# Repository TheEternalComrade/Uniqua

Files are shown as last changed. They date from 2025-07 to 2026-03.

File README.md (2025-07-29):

# Uniqua
Uniqua is very cool pen plotter. She has 2 y-axis' to increase stability, limit switches for automatic homing, and a very good sense of style.
This is the most complex project I have ever undertaken, despite the relatively off-the-shelf electronics setup. The CAD is completely custom

## CAD


## Wiring


Credits to [Krishna Kumar](https://www.hackster.io/kk1211114) for the diagram

## BOM
| Name | Purpose | Source | Price | Link | Total|
|:---|:---|:---|:---|:---|:---|
|6pcs 8*400 Linear Rods|For bearings to slide on|Amazon|$27|[link](https://www.amazon.com/gp/product/B0CXTX5FZ3/ref=ox_sc_act_title_1?smid=A2IW11PEFKCHE9&psc=1)||
|Power Supply|To give arduino power|Amazon|$7.50|[link](https://www.amazon.com/gp/product/B018OLREG4/ref=ox_sc_act_title_3?smid=A2VN47FGA6FR8&psc=1)||
|GT2 stepper motor pulley|To hold belt|Amazon|$6|[link](https://www.amazon.com/gp/product/B07CXSSGF8/ref=ox_sc_act_title_4?smid=A2QQQKMKGVNA5E&psc=1)||
|Linear ball bearings|To enable smooth movement of gantries|Amazon|$12|[link](https://www.amazon.com/gp/product/B087WPGQ8T/ref=ox_sc_act_title_5?smid=A3TIH0U3DL7GNQ&psc=1)||
|Taxes|So the government gets a cut too|Amazon|$1.9|none||
|SG90 Servo| To lift pen|Aliexpress|$2.31|[link](https://www.aliexpress.com/item/3256806385982254.html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)||
|FTM Jumper Cables|To connext electronics wires|Aliexpress|$2.90|[link](https://www.aliexpress.com/item/3256802798368625.html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)||
|Arduino Uno Clone(extra in case of malfunction)|The brains|Aliexpress|$9|[link](https://www.aliexpress.us/item/3256805955372826.html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)||
|GT2 Idler pulley|To hold belt|Aliexpress|$3.51|[link](https://www.aliexpress.com/item/3256805966224219.html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)||
|M3 x 16 screws|to hold stepper motors|Aliexpress|$1.19|[link](https://www.aliexpress.com/item/3256805692722422.html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)||
|M5 x 20 screws|to hold idler pulleys|Aliexpress|$1.79|[link](https://www.aliexpress.com/item/2255800598515019.html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)||
|Stepper motor driver|to drive stepper motors|Aliexpress|$6.30|[link](https://www.aliexpress.com/item/3256803799187214.html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)||
|CNC shield| has all the works for safe cnc-ing|Aliexpress|$2.33|[link](https://www.aliexpress.us/item/3256806291794239.html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)||
|4 x 100 linear rod|For the pen holder to slide up|Aliexpress|$4.26|[link](https://www.aliexpress.com/item/3256804855023250.html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)||
|Limit switch|Automatic homing|Aliexpress|$1.58|[link](https://www.aliexpress.com/item/3256805410237576.html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)||
|M5 washers|So pulleys don't directly touch the plastic|Aliexpress|$1.68|[link](https://www.aliexpress.com/item/3256807003597592.html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)||
|m5 hex nuts|for m5 screws |Aliexpress|$2|[link](https://www.aliexpress.com/item/3256808093729366.html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)||
|gt2 timing belt|to move gantries|Aliexpress|$3.6|[link](https://www.aliexpress.com/item/3256808671441858.html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)||
|nema 17 stepper motor|to move belts|Aliexpress|$12.9|[link](https://www.aliexpress.com/item/3256805095424554.html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)||
|M8 x 500 threaded rod|To enhance stability|Aliexpress|$14.7|[link](https://www.aliexpress.com/item/3256807919274570.html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)||
|5 x 15 Spring|For more consistent pen contact|Aliexpress|$2.43|[link](https://www.aliexpress.com/item/3256807406561228.html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)||
|m8 hex nuts|for m8 rods|Aliexpress|$2.43|[link](https://www.aliexpress.com/item/3256807407546447.html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)|
|*m2 x 10 screw|For pen lift mechanism and fastening limit switches|Aliexpress|$~1.5|none||
|*m2 x 3 heatset inset|For holding screws|Aliexpress|~$1.5|none||
|Taxes|governments|Aliexpress|$6|||
||||||$134.88|

*Already have these

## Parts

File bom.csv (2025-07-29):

Name | Purpose | Source | Price | Link | Total
6pcs 8*400 Linear Rods | For bearings to slide on | Amazon | $27 | link
Power Supply | To give arduino power | Amazon | $7.50 | link
GT2 stepper motor pulley | To hold belt | Amazon | $6 | link
Linear ball bearings | To enable smooth movement of gantries | Amazon | $12 | link
Taxes | So the government gets a cut too | Amazon | $1.9 | none
SG90 Servo | To lift pen | Aliexpress | $2.31 | link
FTM Jumper Cables | To connext electronics wires | Aliexpress | $2.90 | link
Arduino Uno Clone(extra in case of malfunction) | The brains | Aliexpress | $9 | link
GT2 Idler pulley | To hold belt | Aliexpress | $3.51 | link
M3 x 16 screws | to hold stepper motors | Aliexpress | $1.19 | link
M5 x 20 screws | to hold idler pulleys | Aliexpress | $1.79 | link
Stepper motor driver | to drive stepper motors | Aliexpress | $6.30 | link
CNC shield | has all the works for safe cnc-ing | Aliexpress | $2.33 | link
4 x 100 linear rod | For the pen holder to slide up | Aliexpress | $4.26 | link
Limit switch | Automatic homing | Aliexpress | $1.58 | link
M5 washers | So pulleys don't directly touch the plastic | Aliexpress | $1.68 | link
m5 hex nuts | for m5 screws | Aliexpress | $2 | link
gt2 timing belt | to move gantries | Aliexpress | $3.6 | link
nema 17 stepper motor | to move belts | Aliexpress | $12.9 | link
M8 x 500 threaded rod | To enhance stability | Aliexpress | $14.7 | link
5 x 15 Spring | For more consistent pen contact | Aliexpress | $2.43 | link
m8 hex nuts | for m8 rods | Aliexpress | $2.43 | link
*m2 x 10 screw | For pen lift mechanism and fastening limit switches | Aliexpress | $~1.5 | none
*m2 x 3 heatset inset | For holding screws | Aliexpress | ~$1.5 | none
Taxes | governments | Aliexpress | $6
 |  |  |  |  | $134.88

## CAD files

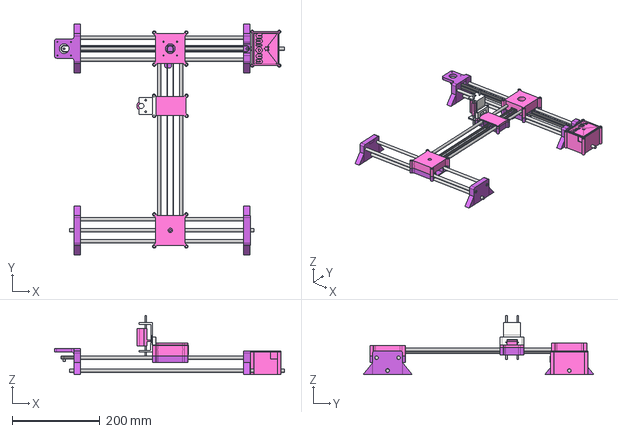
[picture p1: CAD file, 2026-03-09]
The-Scheme-Machine.step
524.0 x 526.0 x 134.4 mm

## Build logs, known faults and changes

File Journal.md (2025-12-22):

---
title: "Uniqua"
author: "@Ayo"
description: "A pen plotter for plotting schemes!"
created_at: "2025-05-30"
---

#Total Time Spent: 37 hours

## May 30, 2025
Today, I started brainstorming. Imma be honest, I feel completely out of my depth with this one.
With a keyboard, there are plenty of resources, and I had completed Hackpad before to boot.

I'm not sure where to start. 

So, I've taken to gobbling up every resource I can find about pen plotters.

Here are some I've found so far:

From Aliexpress


By [SuperbTech](https://www.instructables.com/member/Superb+Tech/)



By [Dejan](https://howtomechatronics.com/author/howtom12_wp/)

Learning about and examining these designs, I'm starting to see a rough bill of materials:
- 2 stepper motors for the x and y axis
- A servo motor to lift and place the pen
- 6 linears rods, 4 for the y axis, 2 for the x axis
- 4 to 8 linear ball bearing(these are kinda expensive)
- 2 stepper motor drivers
- A CNC shield
- A elegoo uno(cheaper than arduino)
- A 12v power supply

One resource I found particularly helpful was [this plotter](https://www.youtube.com/watch?v=z4_OFkAW_JY&ab_channel=CreativityBuzz) 
designed with wood instead of plastic parts. I found that the design was a lot simpler without any of the frills plastic parts had. 
This was extremely useful in helping me get an idea of how to design the toolhead.

After a lot of YouTube videos, I sketched out a more detailed plan for The Scheme Machine. I wish I could say I had an intuitive goal for this, like I had convenience
for The Prince Keeb, but I just want this to work TT.



Time Spent: 5 hours

## June 4, 2025
I've placed the first item in my 3d model! A humble Nema 42-40 stepper motor.


Next, I want to place a pulley, but I realized I didn't know what size it needed to be. After looking at what other models used, I decided to go with a timing belt with a width of 6mm and a pitch(think wavelength) of 2mm, which means I need GT2 pulleys that also have a width of 6mm. I also need to figure out how high or low the pulley will be on stepper motor shaft. Looking through the Blot assembly guide, it seems top of the pulley should be flush with the top of the shaft.


Now that I've got my first motor and pulley figures out, I s'pose its time to actually model some original parts. I want to create a sort of stand that will screw into the stepper motor, and also hold 2 of the y-axis linear rods. But, I shall procrastinate that until tommorrow.

Time Spent: 1 hour

## June 8, 2025
I spent so much time fiddling with CAD software today. For some context, I use laptop. This laptop runs Windows, and for some wack-ahh reason, Fusion360 has basically no touchpad support for it. The only think I can do reliably is zoom in and out.

So, I decided to try out FreeCad. While it does have pretty good touchpad support, it's very different from Fusion360 and I felt really uncomfortable using it.

I eventually went back to Fusion360, and it turns out it actually does have touchpad support, though it's a really weird method.

I started designing the part that will sit on the y-axis stepper motor and will hold some of the y-axis linear rods. They're very rough rn, but I hope to make 'em look better in the future.


Time Spent: 1 hour

## June 13, 2025
Today, I built more of my first y-axis section. 

<i>Isn't it neat?</i>

Funny story! For a while, I looked for a 3d model of linear rods of the size I needed for this. Then, I realized that I could just draw  8mm circle, and extrude it to the desire length. Convenient! 

I also started desiging the first y-axis gantry. I had to spend some time figuring out how the linear ball bearings would fit.
(insert screenshots here)




Ultimately, I came up with a two-part deisgn where the bottom half of the gantry holds the bottom half of the linear ball bearings and the y-axis belt clip, while the top half of the gantry holds the top half of the bearings, has screw holes for the x-axis stepper motor, and holds the x-axis linear rods .

While I was trying to deign the y-axis belt clip, I realized I didn't quite know how close it would be to the ball bearings. So, I went through the painstaking process of designing my own in the project. 

<i>Belt!</i>

I think I'm done for today. Next session, I'll work on actually designing the belt clip, and the top part of the gantry. 

Time Spent: 3 hours

## June 14, 2025
Today, I did a lot of work on the y-axis gantry.

The thing that probably took me the most time was figuring out how the belt would be positioned.

I was originally going for a thin wedge for it, until I realized it needed to have teeth to match the belt. I tought about using zip ties, but I don't want to add more expense to this project. Since I'm not that confident in my 3d modeling skills, I settled on this loop design, where teeth of the belt latch onto each other:


I still need to edit this a bit to ensure the bearing's stability, but I think it's pretty decent so far

I also started working on the top part of the gantry. It took embarrassingly long amount time to figure out how to position it.

This is what it looks like so far:


Since working on this is literally giving me a headache, Imma call it quits till next week. Next time, I wanna develop the top part of the y-axis gantry so that it can hold linear rods, a stepper motor pull, and the x-axis timing belt.

Time Spent: 4 hours

## June 16, 2025
So I decided to completely redesign my y-axis gantry.

<i>Gantryless y-axis</i>

I increased the spacing between the y-axis linear rods, because I realized doing so would allow the x-axis motor to fit better on the y-axis gantry. The dimensions of the stepper motors I plan on using are 42mmx42mm, while the spacing between the rods was previously 36mmx36mm

I'm quite pleased with the general idea of my gantry, though I will have to go over an beautify it later on for taste.


This is what Uniqua looks like rn! Did I mention I named my pen plotter Uniqua?


Time Spent: 2 hours

## June 28, 2025
Ok, so for some reason, I think one of my journal entries didn't save. What a shame. I don't quite remember what I wrote, but I will provide a rough summary based on the changes from the most previous picture.

I realized that the idler pulleys do not have to be at the tippy top of the motor shaft, so I moved them down exactly 4.5mm. This allows the belt clips to be level with the linear bearing slots. This also reduces the height of the y-axis gantry by by allowing the x-axis stepper motor be placed lower.



I also completed most of the top part of my y-axis gantry.



Today, I started designing my pen gantry. 


<i>Sure it's just 2 linear bearings, but it's got vision</i>

I also plotted and planned how I'd attach the two halves of the y-axis gantry. Or more specifically, where I'd put the screw holes. It was surprisingly difficult, as I have to make sure the screw dont effect the belts, stepper motors, linear rods, etc.

Time spent: 1 hours

## July 10, 2025
It's been 12 days since I've worked on this project.

I think I'm going to add limit switches to Uniqua. It would save me the trouble of having to manually home the switches each time I want to print something. The thing is, I'm not quite sure where to place them? I think I'll look at my 3d printer for inspiration.

----

After examinination, I can conclude that the switches just needs to be at the extreme of each axis. 

Then comes the issue of idler pulleys. The main problem of understanding I'm having is how to attach them with minimal friction. Examing my 3d printer, it seems that placing them directly against the plastic should be fine, but I could only see so much from my vantage point.

Time Spent: 1 hour

## July 16, 2025
I've finally decided on the positioning for the y axis idler pulley. It doesn't seem to matter if it's flush with the plastic. But, I might need too add a nut sore something directly above it for stability.



----
I've also completed the main part of the gantry, where the pen will be.


Next, I need to add the mechanisms for the actual penholder.
This is the servo motor, which will be responsible for the lifting of the pen(to avoid stray lines)


I found that in my attempts to make mounting holes for the 2 halves of the pen gantry, I had accidentally made them block the entry of the linear ball bearings


This is what they look like fixed



I'm most likely going to change them a little for greater stability. A note, I'm going to be using heatset inserts instead of screwing them into the plastic directly.

----

I've made a significant portion of my pen holder!



Time Spent: 4 hours

## July 17, 2025

So, I was originally goiing to mount the two halves of the y-axis gantry the same way I mounted the halves of the pen gantry(, as seen above. But I realized it would interfere with the linear ball bearings, so I settled on this mounting option:


I also added some anti-slip protection for the ball bearings



Time spent: 1 hour

## July 21, 2025
Time to add limit switches!!!

After some consideration, I think Im gonna place the x axis limit switch on the pen gantry, and the y axis limit switch on the y-axis gantry.

----
They have been placed!



----

So, I completely forgot that the holes i placed to connect the halves of the y-axis gantry will intersect with the linear rods, so I had to change the design.



----


I've added the linear rods that will be used for the pen lift mechanism. In addition, I've made a significant portion of the actual holder part of the pen holder. I just need to add holes for the tightening screws. The little cylinder is for the servo motor to push up on, though I might have to replace it with a M2 screw for printability. Actually, I'm defintely going to do that.



----
Hole created!



----
Next, I need to add some flair to all the parts and a case for the electronics

Time Spent: 3 hours

## July 22, 2025
I've added the holes for the pen grip, which will allow for a firmer fit. I also increased the length of the penholder part so that a shorter spring can push it down.



----
Upon concerns of stability, I redesigned the holder for the stepper motor so that it can be mounted upside down. This will allow me to use a threaded insert near the bottom.


Time Spent: 2 hours

## July 23, 2025
Today, I spent a bunch of time optimizing my BOM. I had to sligthly shift a part though because I've chosen a new stepper motor.

I'm pretty exciteed because i'm so close to being done!

----

Turns out i accidentally moved the y axis stepper motor too high, which means I had to undo a bunch of work.

----
I finally imported a model of the electronics controller into my CAD. I'm still deciding whether I want this part to be tethered to the rest of Uniqua or not. 
I think I'm pretty much done with the main kinematics system, so I just need to yassify Uniqua and make a case for the controller board.

My progress so far:



Time spent: 3 hours

## July 24, 2025
SHE'S DONE! Or at least, very close to. I think A little yassification is still in order, plus I need to figure out firmware, but other than that, we're pretty good!

I successfully made a case for the controller boards:


This part will be free floating!

So, I think this is the finished cad:


So many hours of work, and finally the end is in sight!

So, Uniqua will need instructions so she can draw pretty pictures like the pretty pretty girl she is. Like parent, like daughter.
Time to learn GRBL I guess. The things we do for our children...

Time Spent: 2 hours

## July 25, 2025
So turn out, GRBL is pretty well documented, so it won't be much trouble to learn. The thing is, I cannot do anything with it until I get the actual parts.
This is the same with UGS, which wil allow g-code(cnc machine code, basically) to be converted to something that a GRBL can read and use to send instructions to the pen plotter.

So, for firmware, I'm probably just going to include g-code for a drawing, or the output from UGS for a drawing.

----
After a bunch of research it seems I need my parent's permission to use Inkscape for generating gcode.
But for now, I used an online svg to gcode converted.

Finally, I'm going to attach the electronic components more pleasantly and prepare this project for submission.

Time Spent: 4 hours

## December 21, 2025
So yeah, it's been quite awhile since I last made an entry. In that time, I've built Uniqua, got her working(I defintely didn't have a million issues), and also lost access to quite a few files on the computer I designed her on. Gosh darn loose power port. Thank the heavens for the people that forced me to upload files to github. I hated it, but look at me now!

To recount the build process I:

* Had to reprint a bunch of parts because hole tolerances were wrong
* Solder a bunch of jumper cable togethers together
* Redesign the pen lift mechanism a couple times, because the bolt I used originally was not cutting it
* Frantically search for a power source as I realized that I NEEDED one for the cnc shield and stepper motors to work
* Wade through many GRBL forks until I found one that supported servos
* DO SO MUCH GOSH DARN GRBL Configuration

And finally, she drew!
https://www.youtube.com/shorts/BBWFe8nOr4c

While Uniqua can draw pretty decently now, there are definitely improvements that can be made. For one, she needs to learn how to write forwards! For another, her legs need to be more stable. A cool idea I hope to explore with Uniqua is handwriting...

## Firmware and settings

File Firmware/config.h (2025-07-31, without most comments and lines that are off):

#define config_h
#include "grbl.h" // For Arduino IDE compatibility.
#define DEFAULTS_GENERIC
#define BAUD_RATE 115200
#define CPU_MAP_ATMEGA328P // Arduino Uno CPU
#define CMD_STATUS_REPORT '?'
#define CMD_FEED_HOLD '!'
#define CMD_CYCLE_START '~'
#define CMD_RESET 0x18 // ctrl-x.
#define CMD_SAFETY_DOOR '@'
#define HOMING_INIT_LOCK // Comment to disable
#define HOMING_CYCLE_0 (1<<X_AXIS)                // REQUIRED: First move X to clear workspace.
#define HOMING_CYCLE_1 (1<<Y_AXIS)  // OPTIONAL: Then move Y at the same time.
#define N_HOMING_LOCATE_CYCLE 1 // Integer (1-128)
#define N_STARTUP_LINE 2 // Integer (1-2)
#define N_DECIMAL_COORDVALUE_INCH 4 // Coordinate or position value in inches
#define N_DECIMAL_COORDVALUE_MM   3 // Coordinate or position value in mm
#define N_DECIMAL_RATEVALUE_INCH  1 // Rate or velocity value in in/min
#define N_DECIMAL_RATEVALUE_MM    0 // Rate or velocity value in mm/min
#define N_DECIMAL_SETTINGVALUE    3 // Decimals for floating point setting values
#define MESSAGE_PROBE_COORDINATES // Enabled by default. Comment to disable.
#define SAFETY_DOOR_SPINDLE_DELAY 4000
#define SAFETY_DOOR_COOLANT_DELAY 1000
#define ACCELERATION_TICKS_PER_SECOND 100
#define ADAPTIVE_MULTI_AXIS_STEP_SMOOTHING  // Default enabled. Comment to disable.
#define TOOL_LENGTH_OFFSET_AXIS Z_AXIS // Default z-axis. Valid values are X_AXIS, Y_AXIS, or Z_AXIS.
#define VARIABLE_SPINDLE // Default enabled. Comment to disable.
#define SPINDLE_MAX_RPM 1000.0 // Max spindle RPM. This value is equal to 100% duty cycle on the PWM.
#define SPINDLE_MIN_RPM 0.0    // Min spindle RPM. This value is equal to (1/256) duty cycle on the PWM.
#define MINIMUM_JUNCTION_SPEED 0.0 // (mm/min)
#define MINIMUM_FEED_RATE 1.0 // (mm/min)
#define N_ARC_CORRECTION 12 // Integer (1-255)
#define ARC_ANGULAR_TRAVEL_EPSILON 5E-7 // Float (radians)
#define DWELL_TIME_STEP 50 // Integer (1-255) (milliseconds)
#if defined(USE_SPINDLE_DIR_AS_ENABLE_PIN) && !defined(VARIABLE_SPINDLE)
  #error "USE_SPINDLE_DIR_AS_ENABLE_PIN may only be used with VARIABLE_SPINDLE enabled"
#endif
#if defined(USE_SPINDLE_DIR_AS_ENABLE_PIN) && !defined(CPU_MAP_ATMEGA328P)
  #error "USE_SPINDLE_DIR_AS_ENABLE_PIN may only be used with a 328p processor"
#endif

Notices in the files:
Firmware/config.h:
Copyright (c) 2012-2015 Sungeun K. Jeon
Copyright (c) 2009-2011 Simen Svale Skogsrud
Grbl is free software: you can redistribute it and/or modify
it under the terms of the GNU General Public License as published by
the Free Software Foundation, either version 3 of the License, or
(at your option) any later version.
